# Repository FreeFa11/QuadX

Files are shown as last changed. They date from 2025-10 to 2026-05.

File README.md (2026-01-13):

# QuadX
A small Drone designed to be simple and cheap and not require a physical controller. It can be controlled by any Smartphone or Computer through Wifi connection using a web browser. 

## Project Outline
- <B>Firmware:</B> Flight Controller and Sensors
- <B>Hardware:</B> Schematic, PCB and 3D Files
- <B>Webpage:</B> Controller Webpage Files

## [Frame](./Hardware/Frame/)

<p align="center">
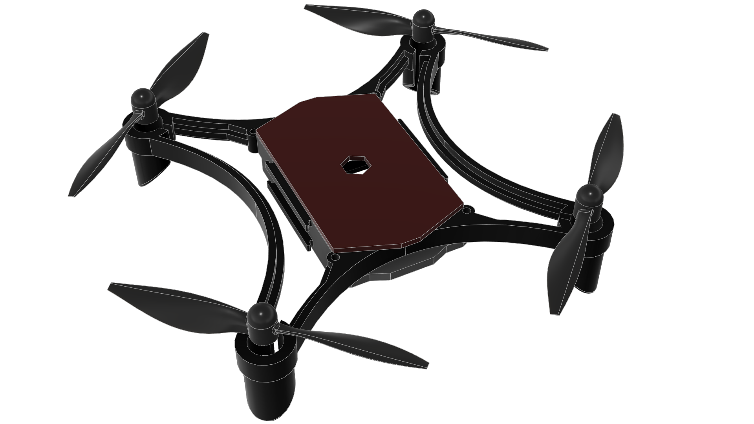
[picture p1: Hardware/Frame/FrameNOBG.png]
    
</p>

3D printed drone frame designed to easily hold 8mm diameter coreless motors and the custom Flight Controller [Board](./Hardware/PCB/).

## [PCB](./Hardware/PCB/)

<p align="center">
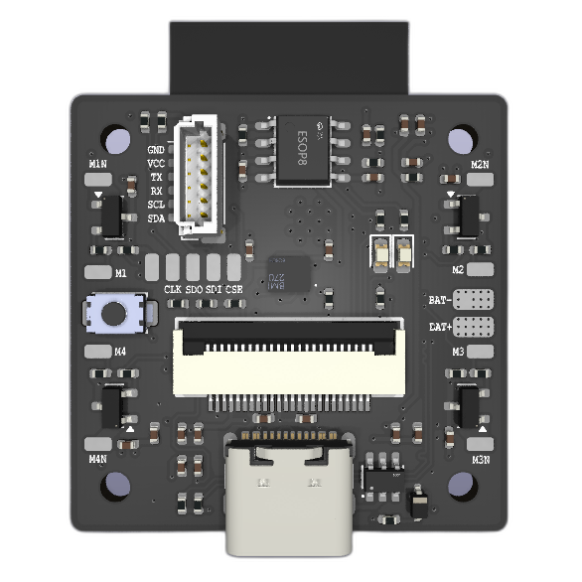
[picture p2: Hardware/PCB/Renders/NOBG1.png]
    
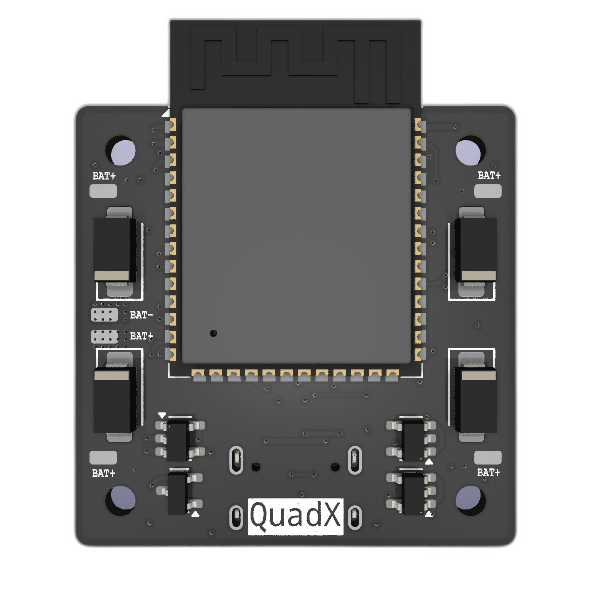
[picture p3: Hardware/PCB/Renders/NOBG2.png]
    
</p>

### Features

- ESP32S3 Microncontroller
- Onboard BMI160 IMU
- Onboard AO3416 MOSFETS
- Onboard Camera Connector
- Onboard 1S Battery Charger

External GPS + Compass module can be connected using the JST-SH (1.00 mm) connector.

## [Firmware](./Firmware/)

The Firmware has been developed using PlatformIO. This Firmware shares a lot of code with my [TwinBlade](https://github.com/FreeFa11/TwinBlade) project.

- **Build**: Open the [Firmware](./Firmware/) folder with PlatformIO installed and build:
  ```
  platformio run
  ```
  Build the filesystem that contains all the required files:
  ```
  platformio run --target buildfs
  ```

- **Flash**: Connect the target microcontroller to flash and run:
  ```
  platformio run --target uploadfs
  ```
  After flashing the filesystem, flash the firmware with:
  ```
  platformi run --target upload
  ```

- **Connect**: After the firmware has been successfully flashed, the microcontroller will act as a Wifi access point with the name `QuadX`. Connect your smartphone to it with password `letsrock`. Open your web browser and type the URL `quadx.local`. This will connect you to the webserver and load the webpage where you can control and modify the drone and its settings.

  *`quadx.local` only works in Wifi AP mode*

<br>

The Web Interface has mostly been completed in terms of functionality. Still needs some work in terms of UI. 
<p align="center">
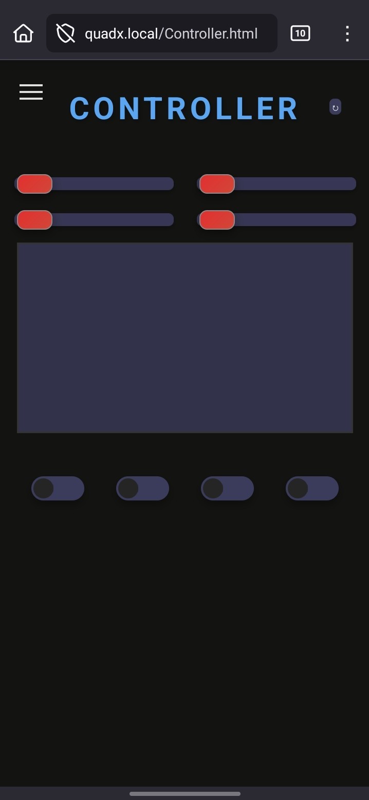
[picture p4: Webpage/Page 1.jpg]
    
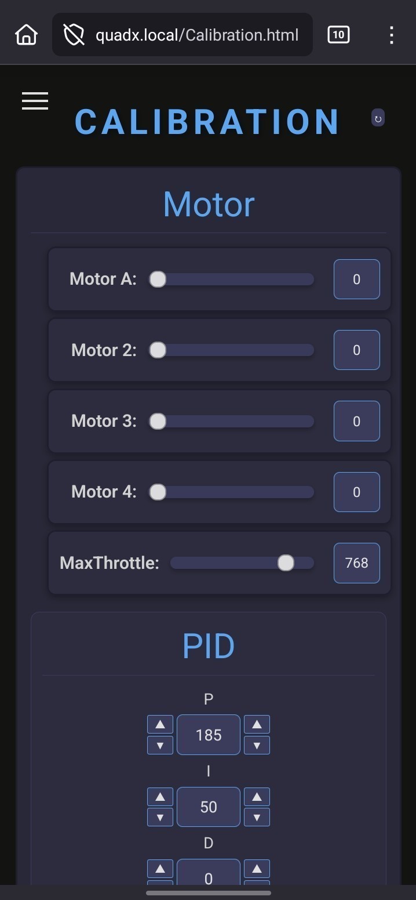
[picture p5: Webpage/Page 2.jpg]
    
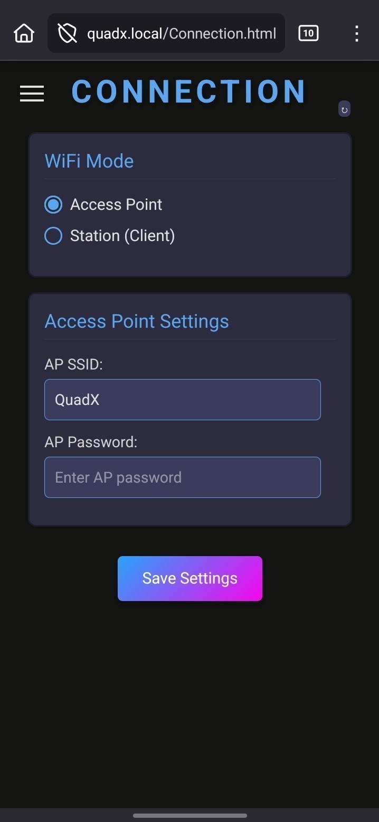
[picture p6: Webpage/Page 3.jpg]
    
</p>

PID gains and controller sensitivity can be easily adjusted from the web interface along with the Wifi settings.

## TODO
- Improve Firmware and Controller
- Real Time Camera Support
- Position and Altitude Hold
- DIY Optical Flow from Camera

## License

All the files in [Hardware](./Hardware/) folder are licensed under [CERN OHL-P v2](./Hardware/LICENSE).

All other files are licensed under [BSD 3-Clause](./LICENSE).

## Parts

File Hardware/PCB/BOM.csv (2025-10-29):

Designator | Footprint | Quantity | Value | LCSC Part #
C1, C10, C11, C12, C13, C17, C19, C2, C4, C5, C8, C9 | C_0402 | 12 | 1uF | C52923
C14, C15 | C_0402 | 2 | 10uF | C15525
C16, C18, C20, C21, C3, C6, C7 | C_0402 | 7 | 100nF | C1525
D1, D2, D3, D4 | D_SMA | 4 | SS34 | C8678
D5 | SOT-23-6_L2.9-W1.6-P0.95-LS2.8-BL-1 | 1 | SRV05-4_C7420376 | C7420376
D6 | D_0603 | 1 | Blue | C2286
D7 | D_0603 | 1 | Red | C2286
D8 | D_SOD-323 | 1 | BZT52C2V7S | C22375298
IC1 | BMI270 | 1 | BMI270
J1, J10, J11, J12, J14, J15, J17, J18, J19, J2, J22, J23, J24, J3, J4, J6, J7, J8, J9 | SolderWirePad_1x01_SMD_1x2mm | 19 | Conn_01x01
J13 | FPC-SMD_24P-P0.50_05A20L24P | 1 | Conn_01x26 | C5362158
J16 | USB_C_Receptacle_GCT_USB4105-xx-A_16P_TopMnt_Horizontal | 1 | USB_C_Receptacle_USB2.0_16P
J20, J21 | SolderWirePad_1x01_SMD_1.5x3mm | 2 | Conn_01x01
J5 | JST_SH_BM06B-SRSS-TB_1x06-1MP_P1.00mm_Vertical | 1 | Conn_01x06_MountingPin
Q1, Q2, Q3, Q4 | SOT-23 | 4 | AO3416
Q5 | Q_SOT-23 | 1 | AO3401A | C15127
R1, R11, R12, R13, R14, R15, R16, R17, R18, R19, R21, R23, R24, R4, R5, R6 | R_0402 | 16 | 10kΩ | C25744
R10, R2, R22, R3, R9 | R_0402 | 5 | 100Ω | C25076
R20 | R_0402 | 1 | 2kΩ | C4109
R7, R8 | R_0402 | 2 | 5.1kΩ | C25905
S1 | SW_TS-1088-AR02016 | 1 | Tactile Button, 160gf | C720477
U1 | SOT-23-5 | 1 | ME6211C28M5
U2 | SOT-23-5 | 1 | ME6211C15M5
U3 | SOT-23-5 | 1 | ME6211C33M5
U4 | ESOP-8_L4.9-W3.9-P1.27-LS6.0-BL-EP | 1 | TP4056 | C16581
U5 | ESP32-S3-WROOM-1 | 1 | ESP32-S3-WROOM-1

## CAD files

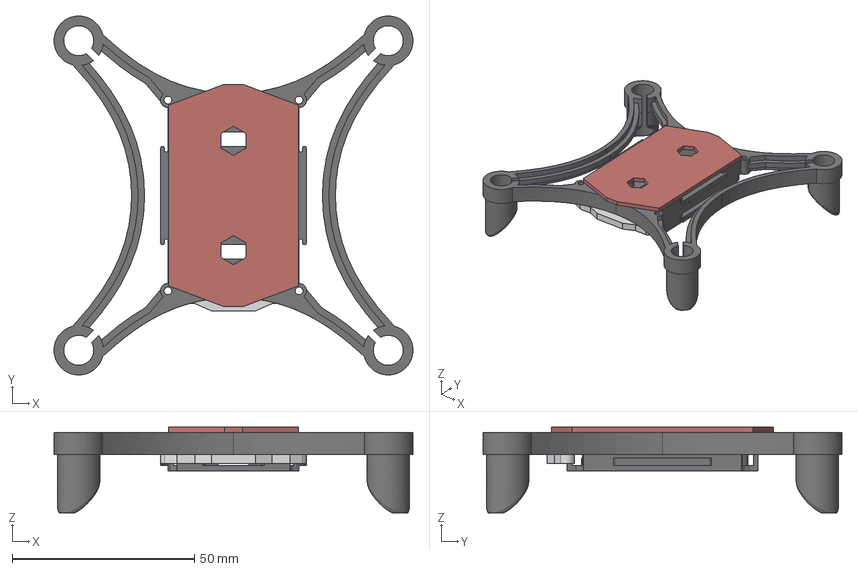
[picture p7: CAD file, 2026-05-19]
Hardware/Frame/Assembled.step
98.6 x 98.6 x 23.5 mm

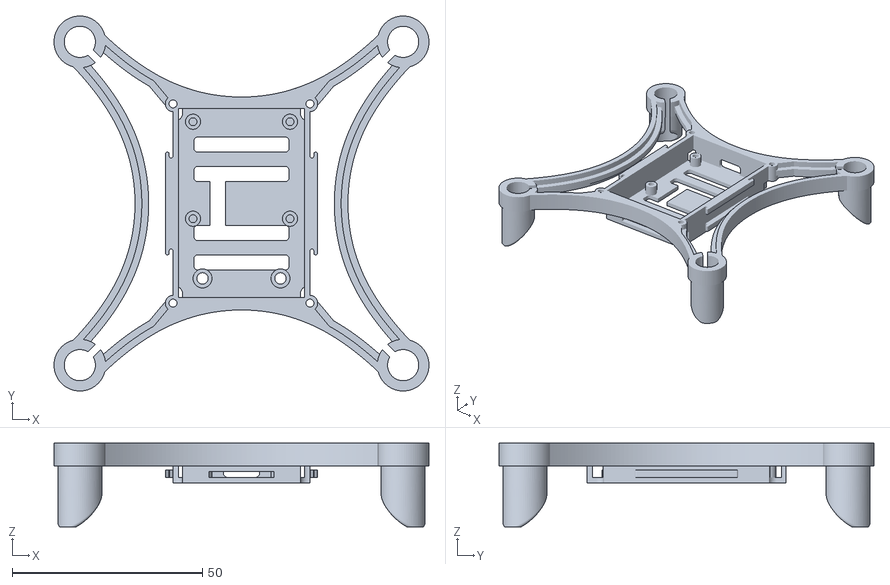
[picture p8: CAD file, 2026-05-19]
Hardware/Frame/Frame.stl
98.6 x 98.6 x 22.0

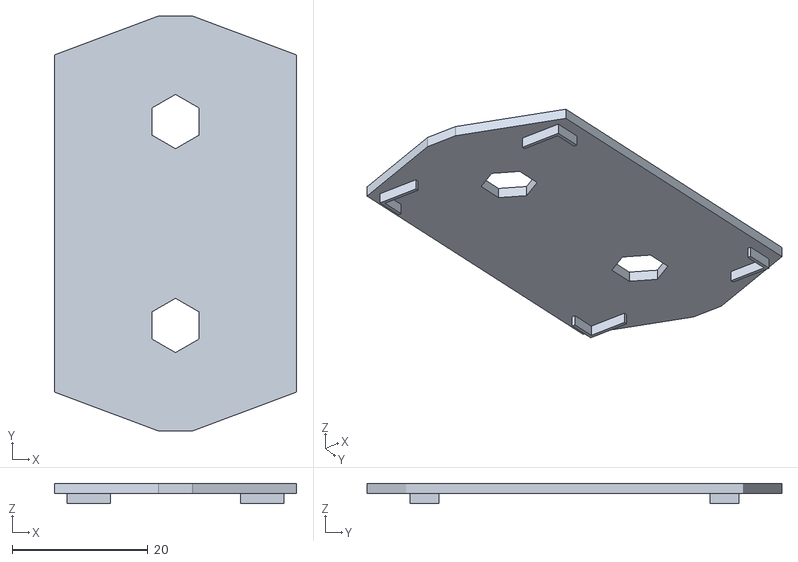
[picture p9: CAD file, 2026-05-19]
Hardware/Frame/Lid.stl
35.7 x 61.1 x 3.00

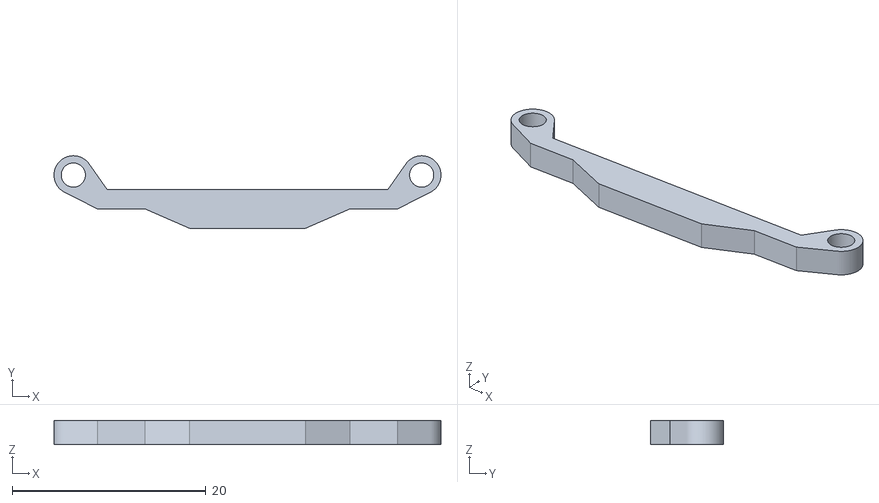
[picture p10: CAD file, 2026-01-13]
Hardware/Frame/Mount.stl
40.0 x 7.50 x 2.50

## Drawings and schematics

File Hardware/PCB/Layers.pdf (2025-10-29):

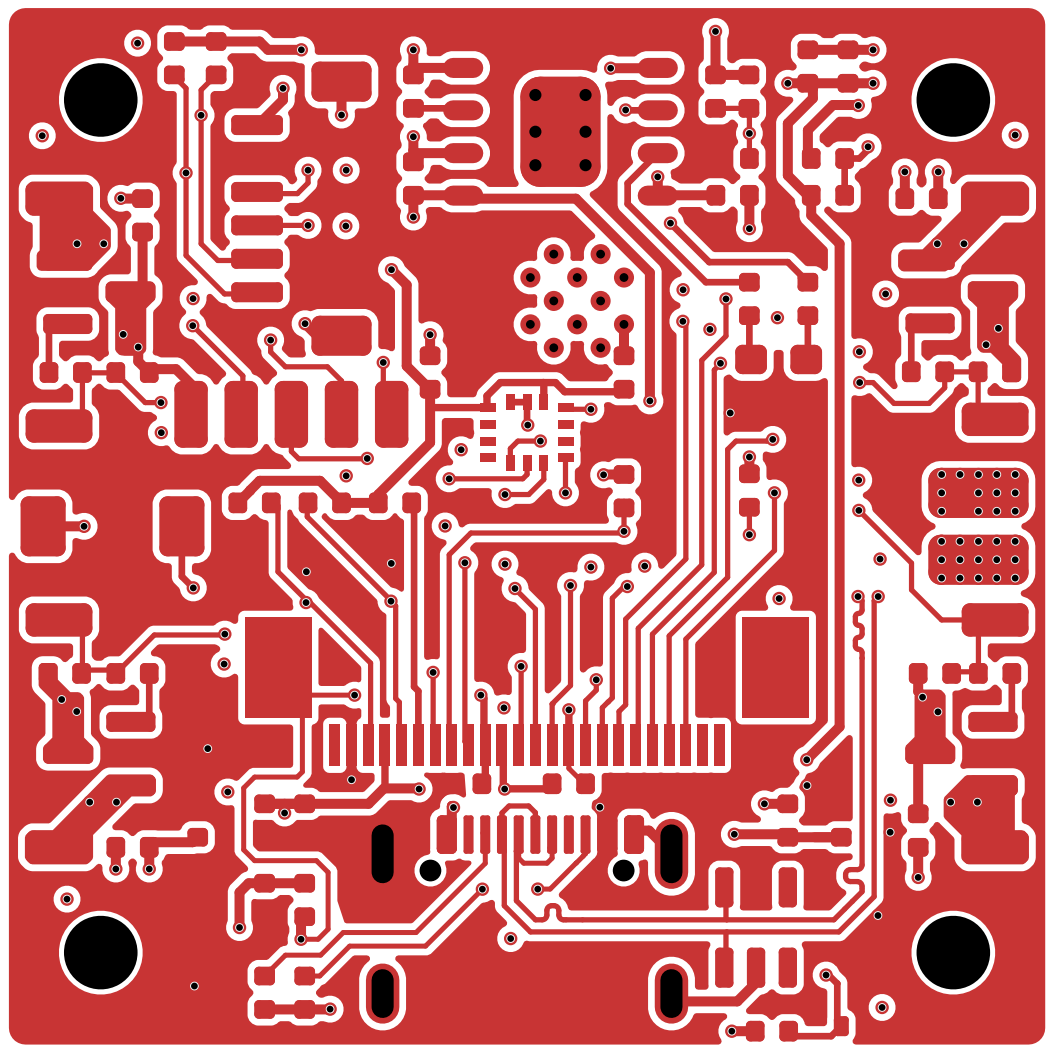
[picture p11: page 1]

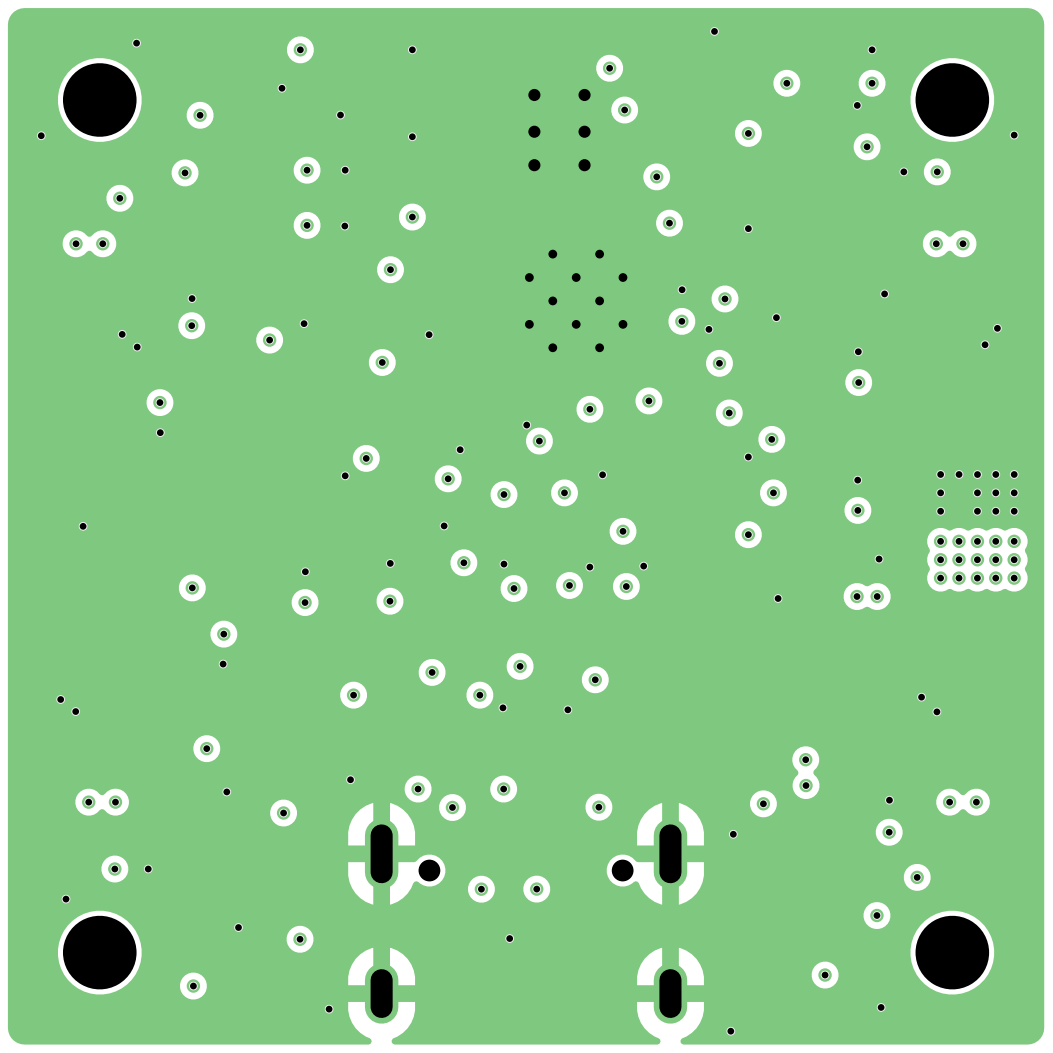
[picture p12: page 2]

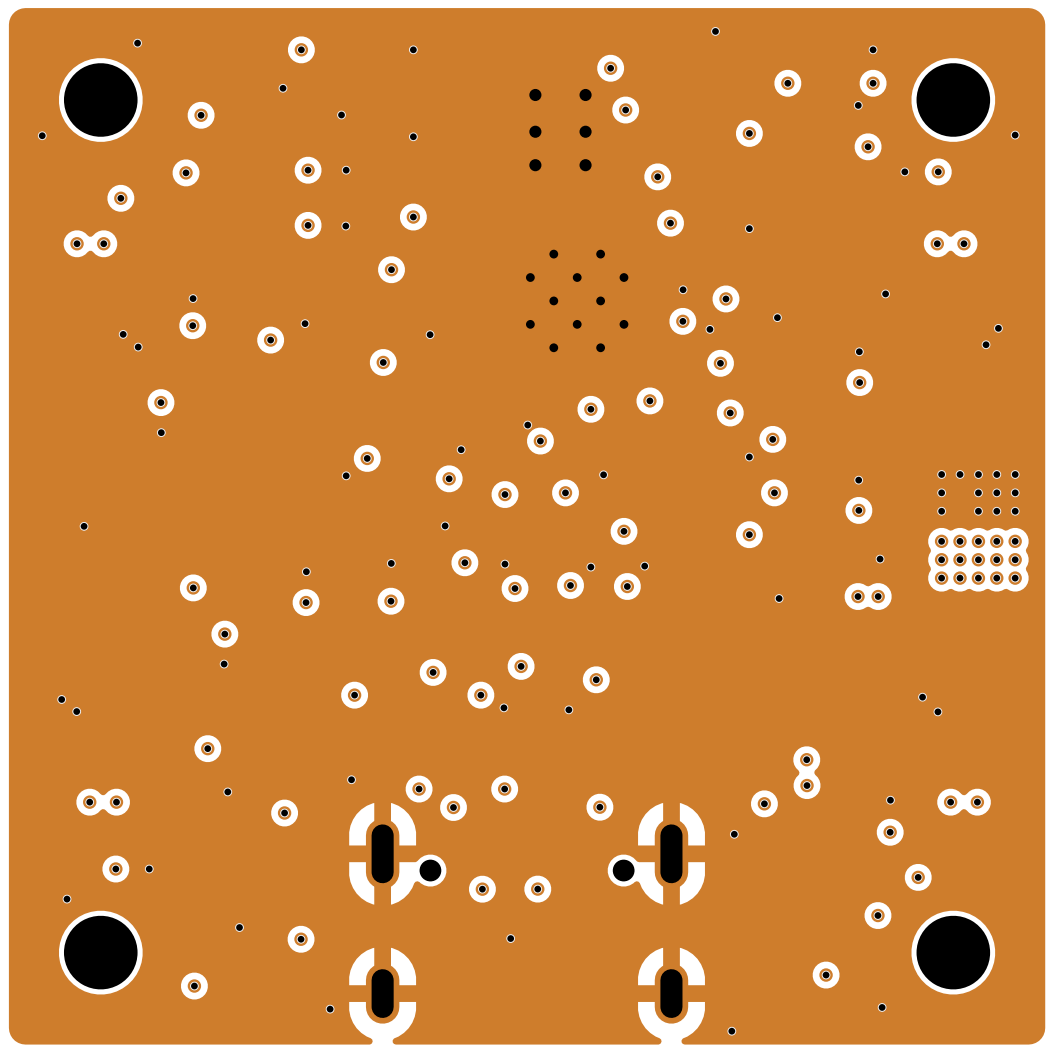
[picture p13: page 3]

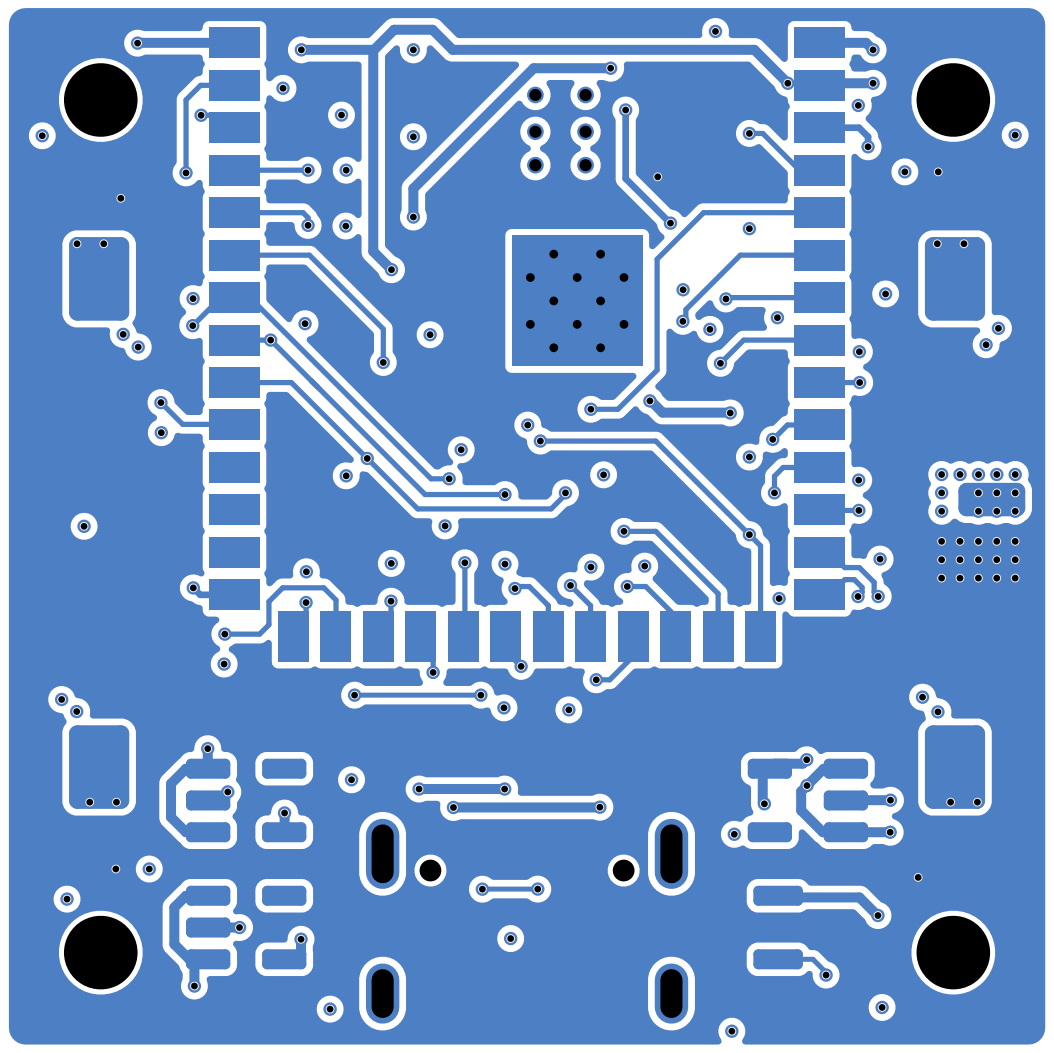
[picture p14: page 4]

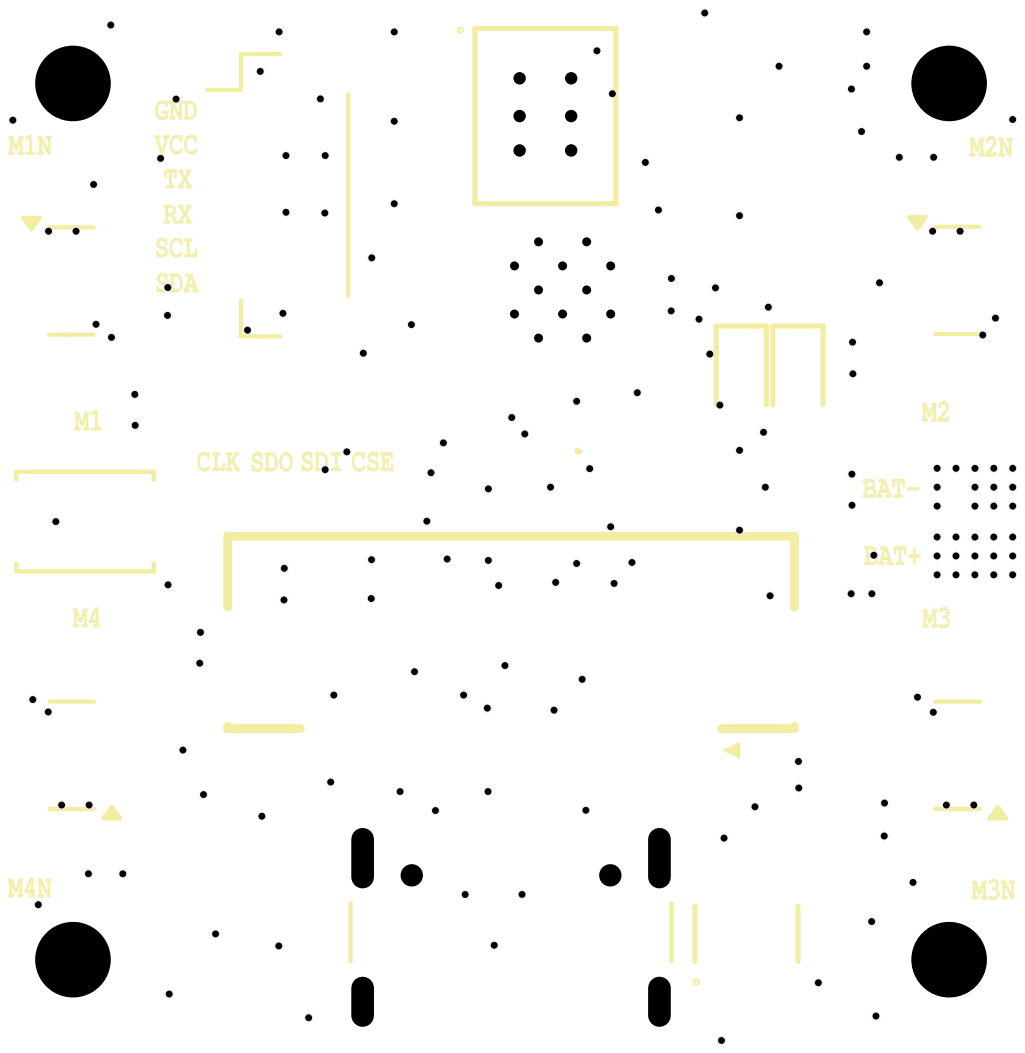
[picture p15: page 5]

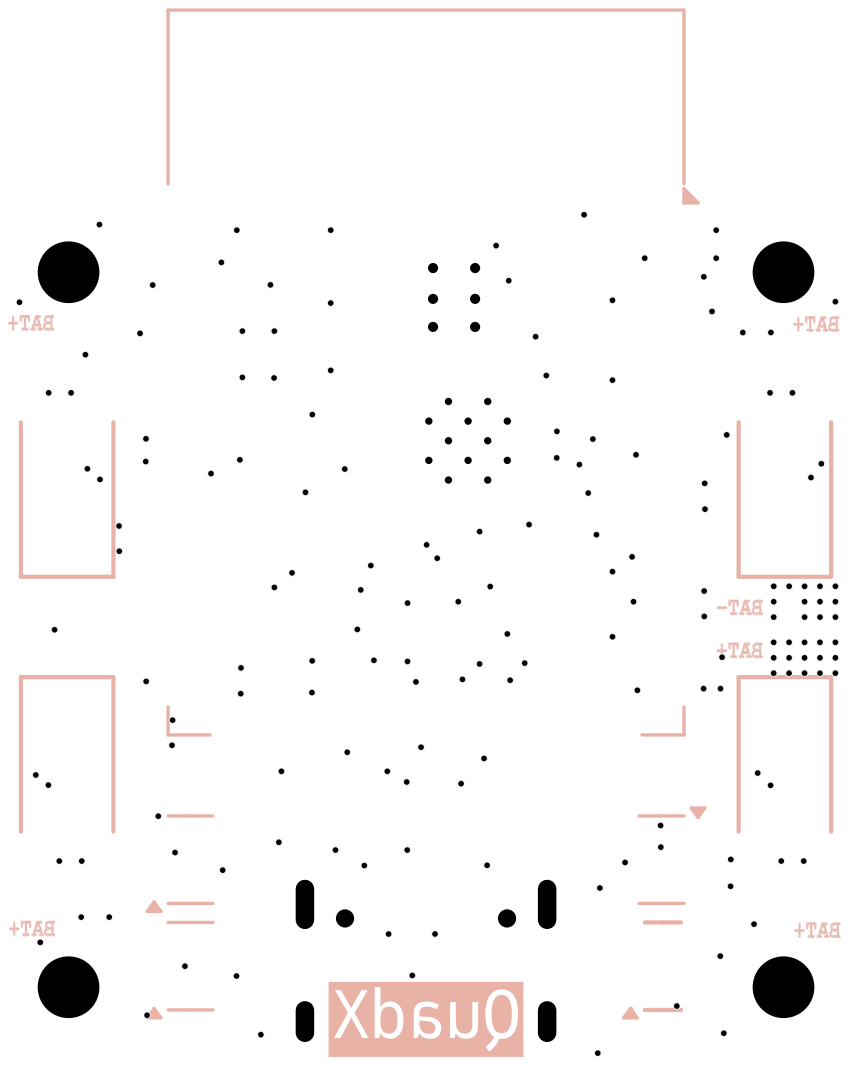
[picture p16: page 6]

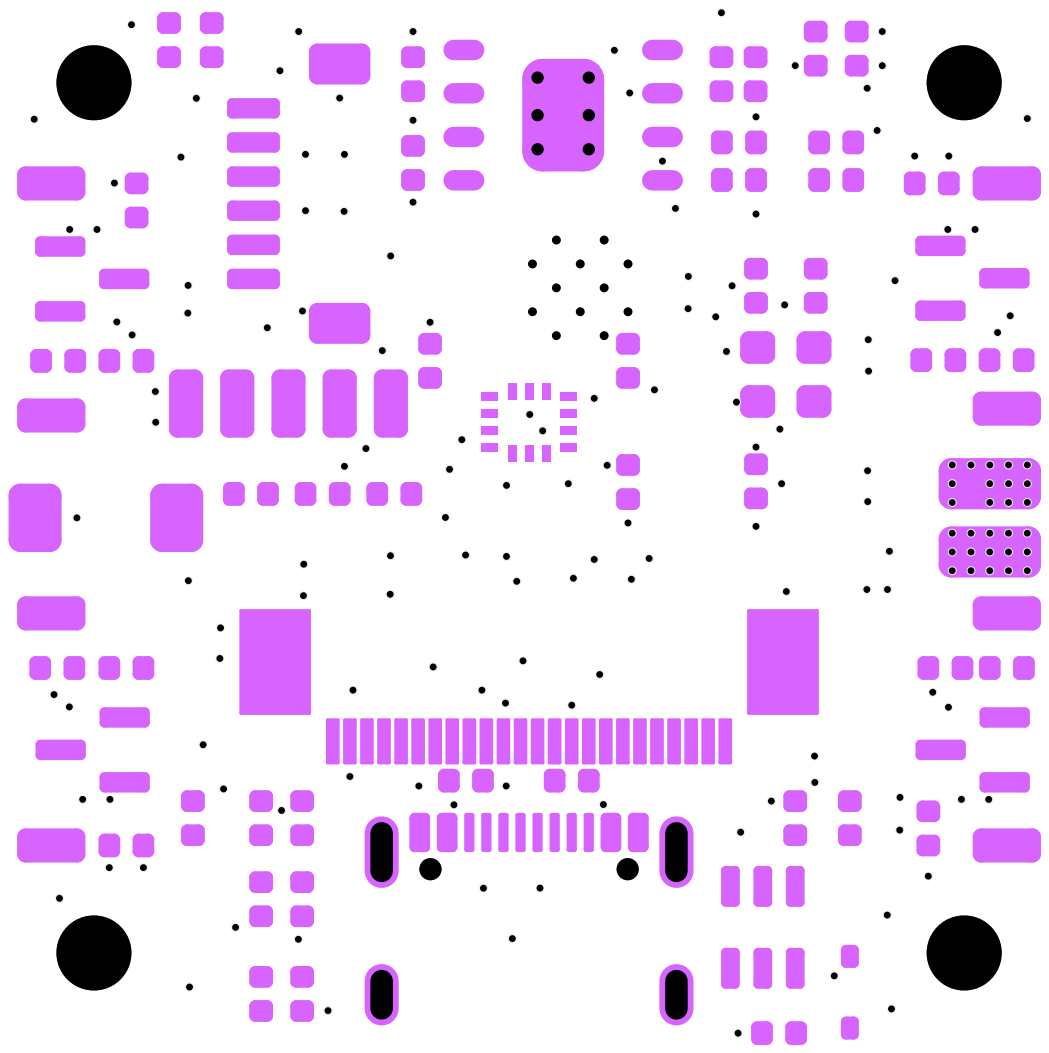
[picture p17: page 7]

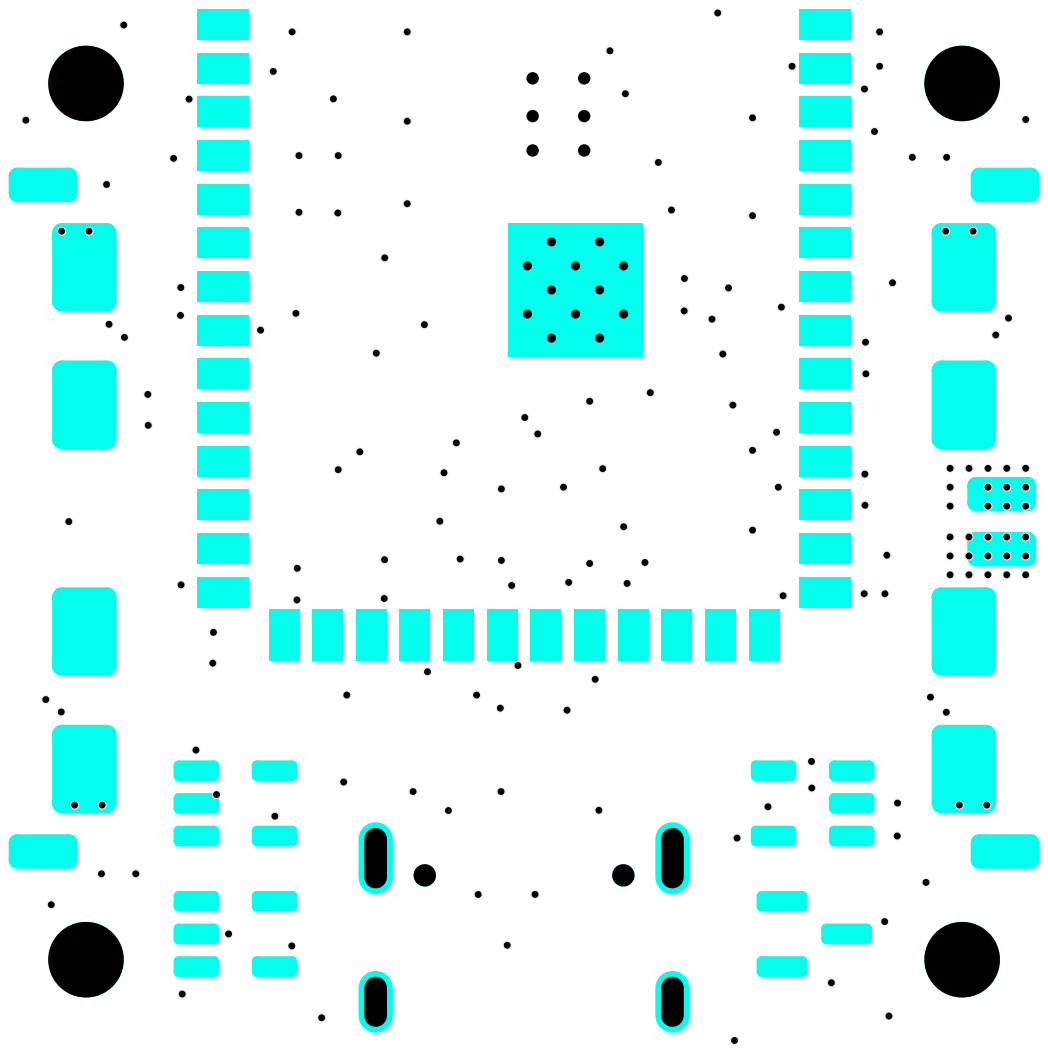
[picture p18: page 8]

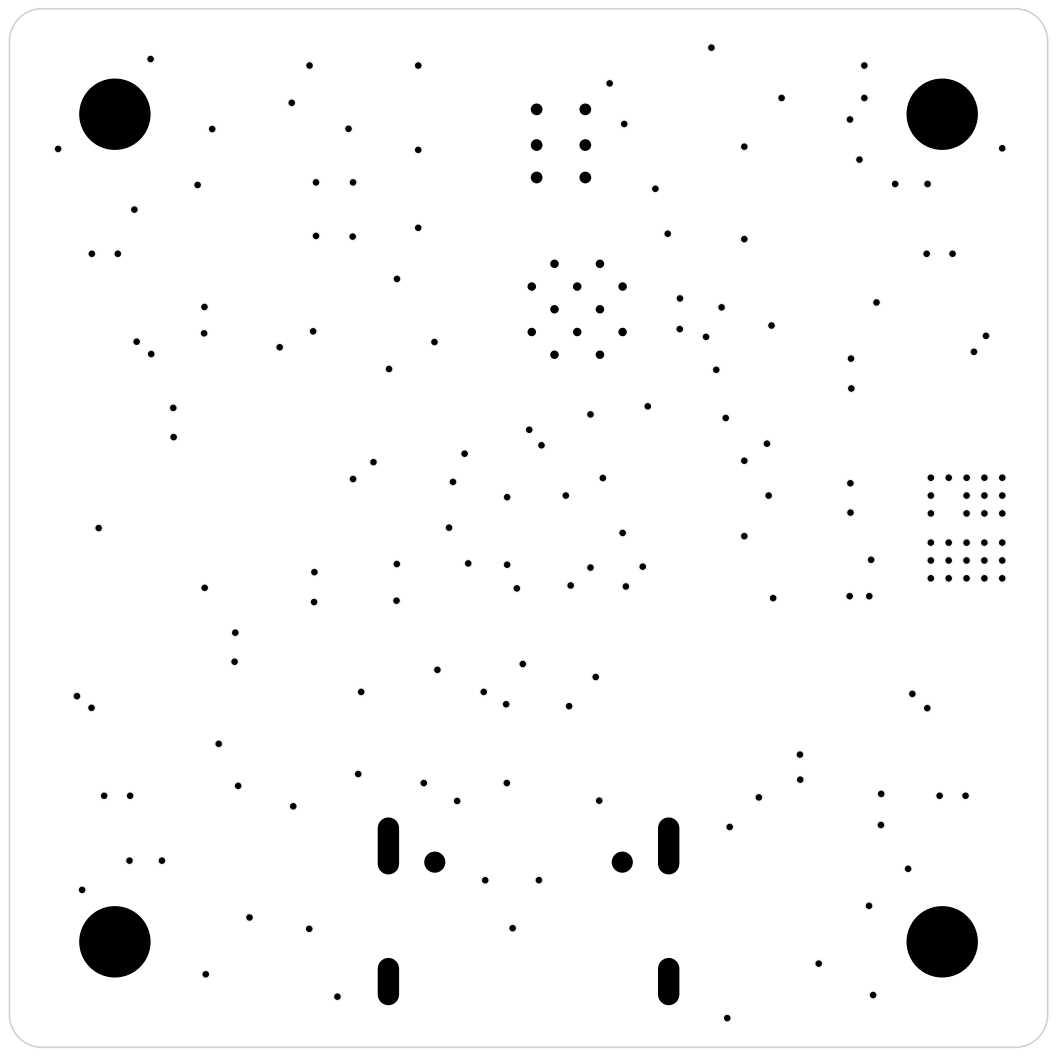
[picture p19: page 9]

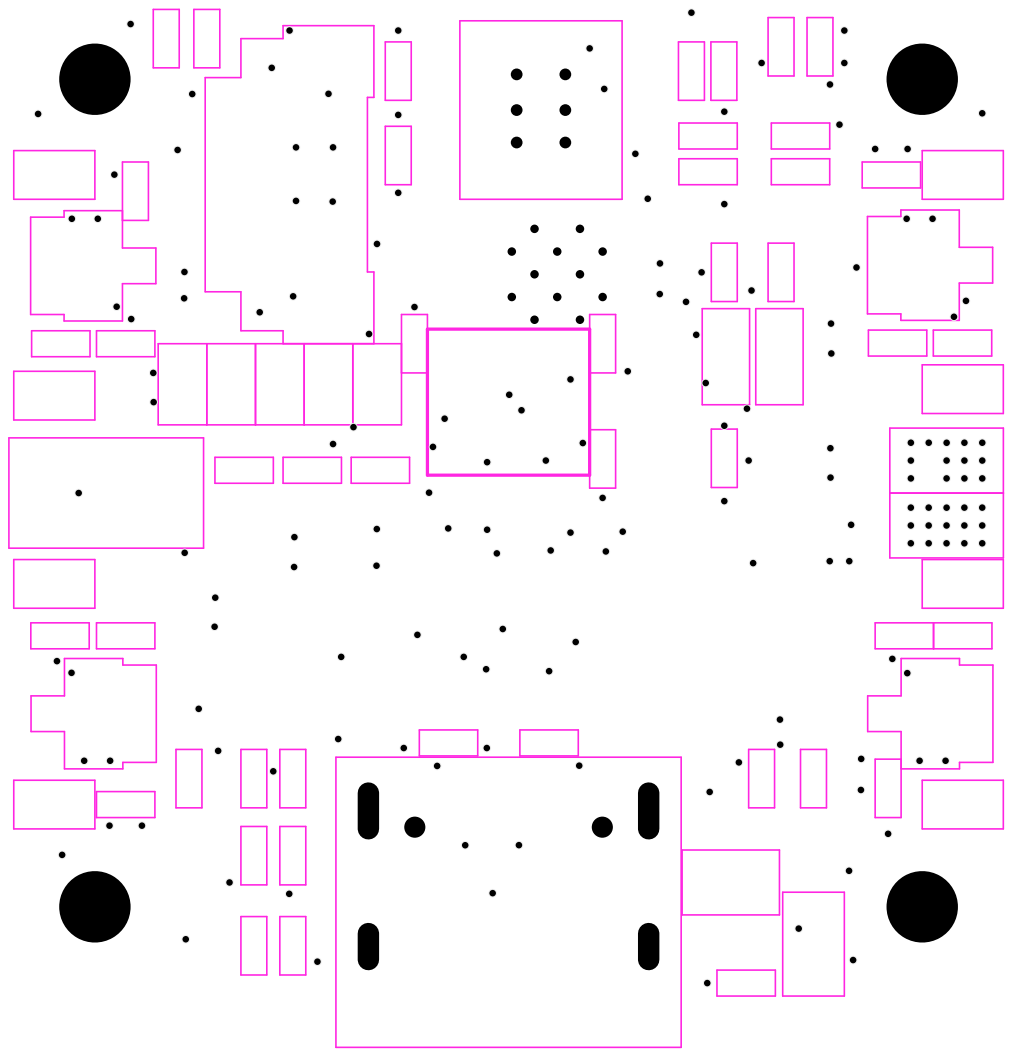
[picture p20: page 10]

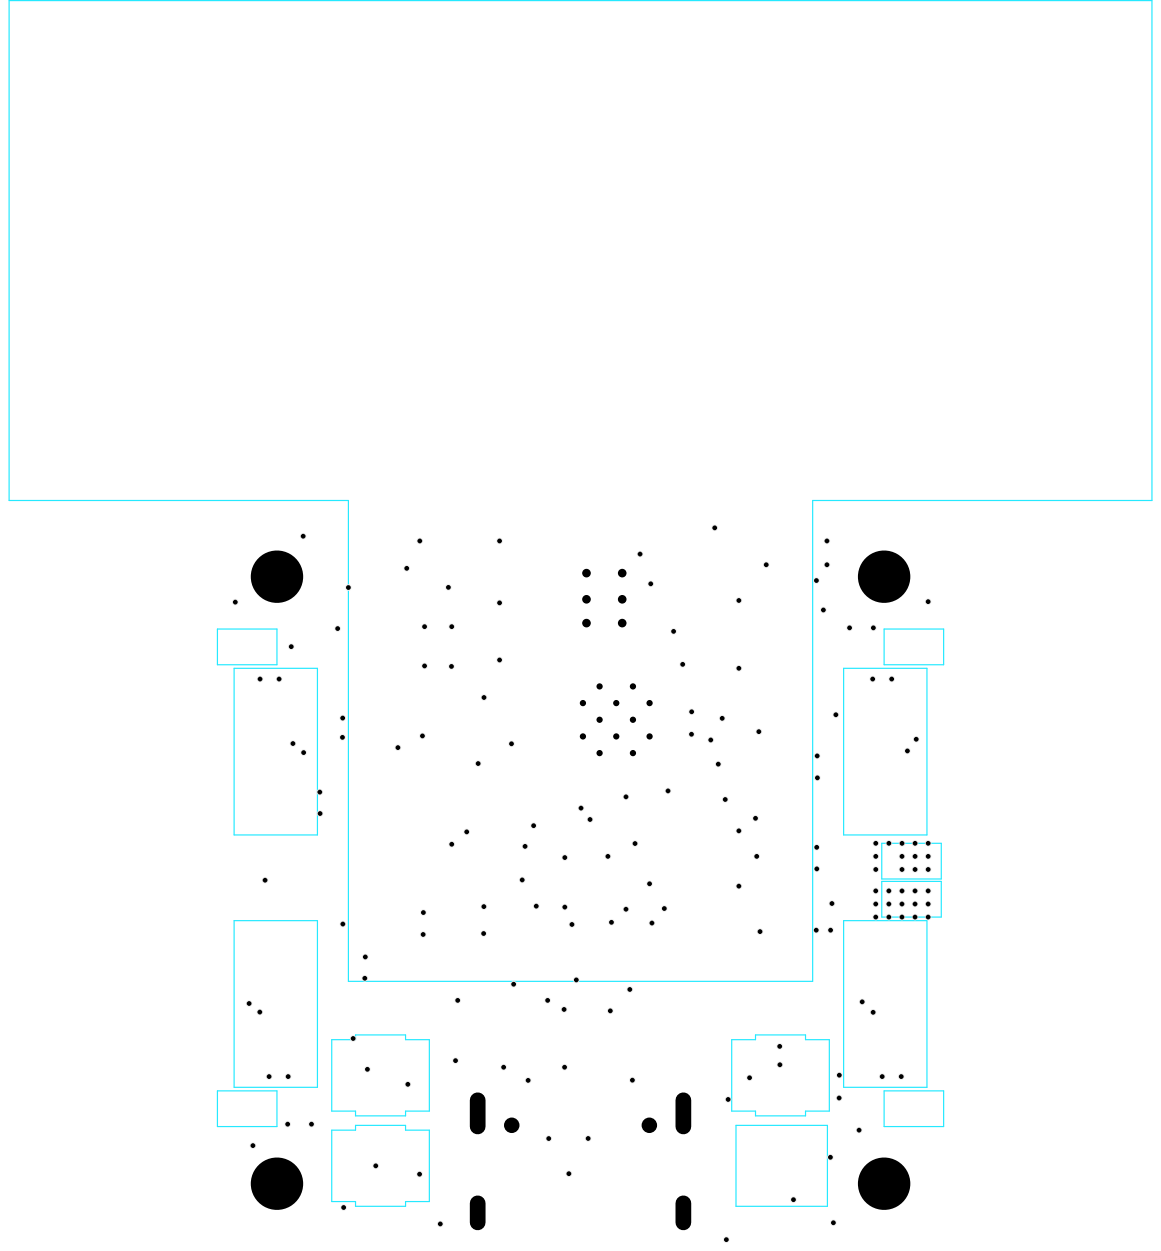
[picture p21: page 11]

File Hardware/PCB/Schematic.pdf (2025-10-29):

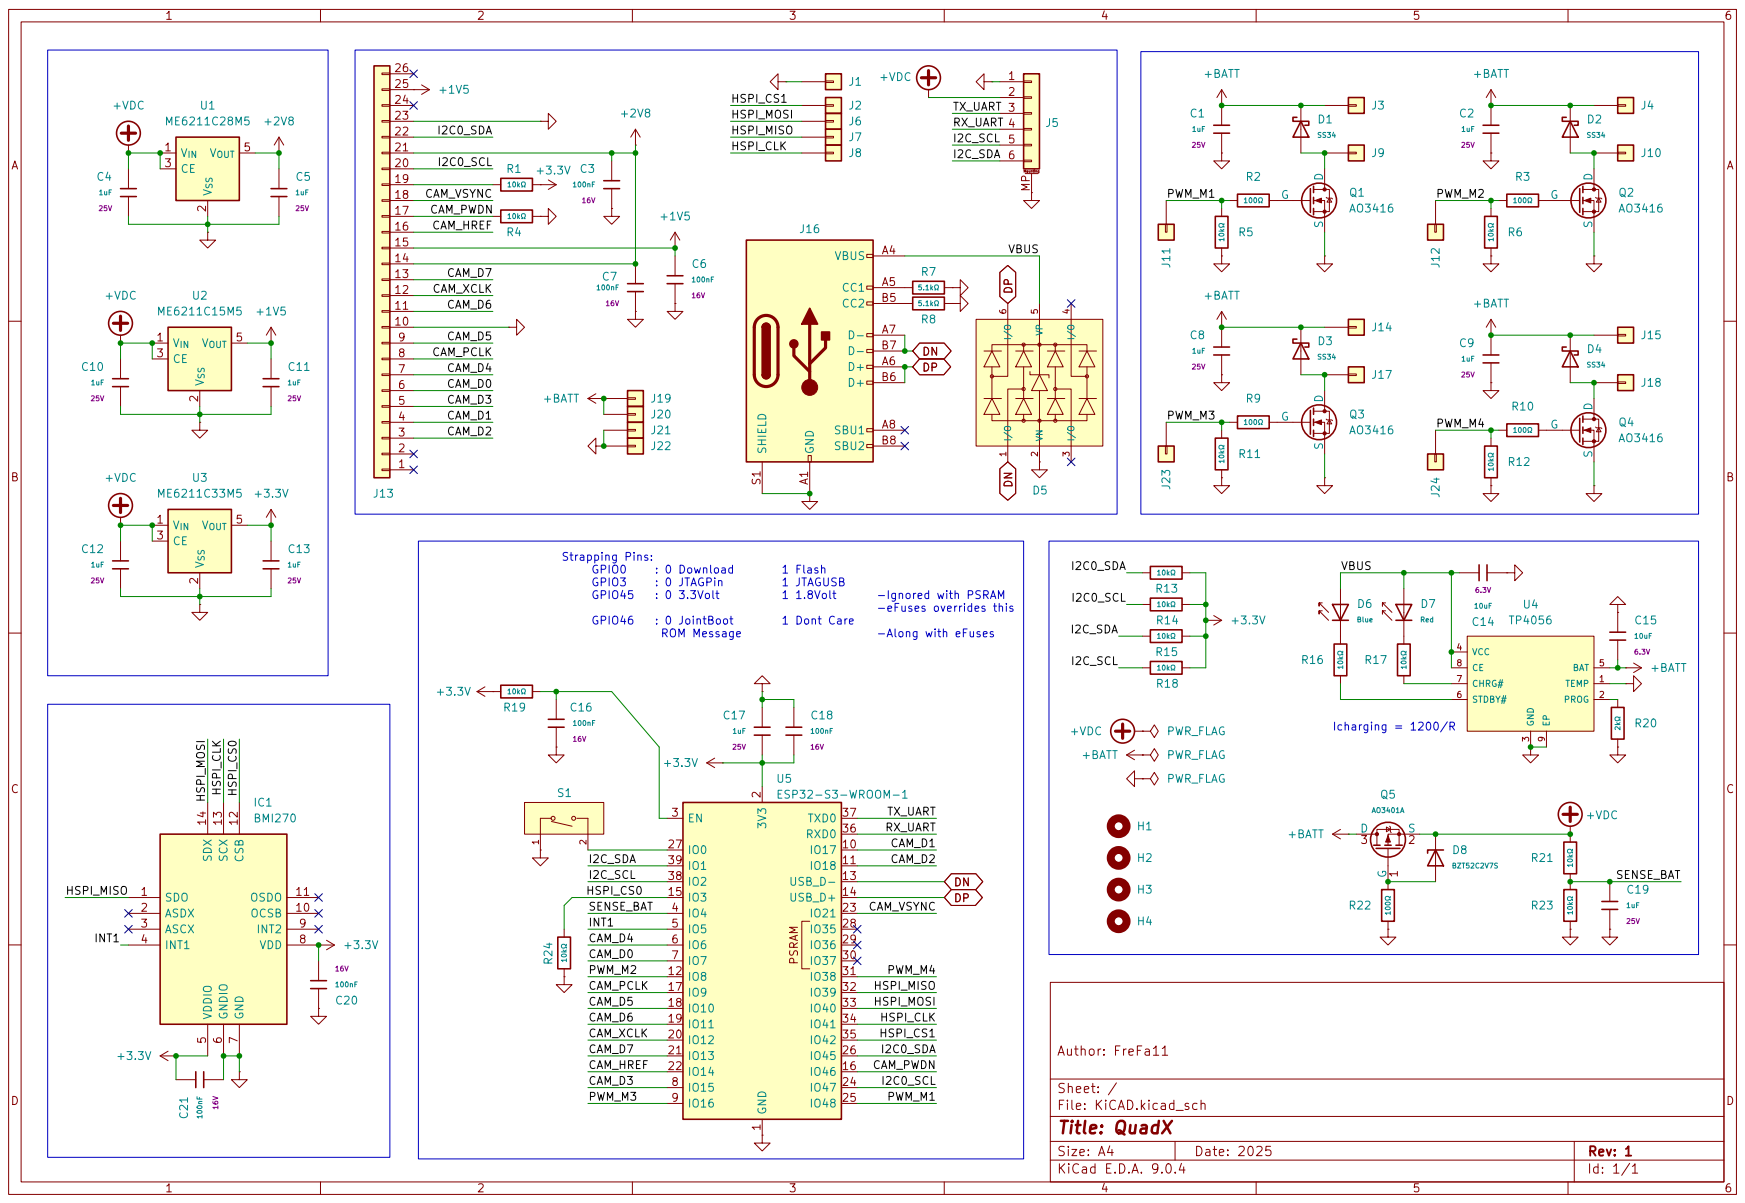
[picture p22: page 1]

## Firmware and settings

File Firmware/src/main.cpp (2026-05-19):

#include <Arduino.h>
#include <freertos/FreeRTOS.h>
#include <USB.h>
#include <LittleFS.h>
#include <Preferences.h>
#include <esp_now.h>

// Modular Codes
#include <Motor.h>
#include <Sensor.h>
#include <Webserver.h>
#include <Transmitter.h>
#include <Control.h>


// Task Handles & Functions
void SystemTask(void *param);
TaskHandle_t ControllerTask;
void Blinky(void *param);
TaskHandle_t BlinkyTask;
hw_timer_t *timer_sensor = NULL;
Webserver droneWebserver;

static void IRAM_ATTR onTimerSensor(){
    BaseType_t xHigherPriorityWoken = pdFALSE;
    vTaskNotifyGiveFromISR(ControllerTask, &xHigherPriorityWoken);
    if (xHigherPriorityWoken == pdTRUE) {portYIELD_FROM_ISR();}
}



// All the Initializations
void setup()
{
  USBSerial.begin(115200);
  LittleFS.begin();

// Wifi & Server
  droneWebserver.StartWiFi();
  droneWebserver.StartWebserver();

  // Transmitter
  StartReciever();

  // Test Sensor
  // Sensor<float> droneSensor;
  // droneSensor.InitializeIMU();
  // droneSensor.InitializeBARO();
  // droneSensor.StartSensors();
  // while(true){delay(1000);}


//  Tasks
  // xTaskCreatePinnedToCore(
  //   Blinky,
  //   "Blinky",
  //   1000,
  //   NULL,
  //   3,
  //   &BlinkyTask,
  //   0
  // );

  
  xTaskCreatePinnedToCore(
    SystemTask,
    "SystemTask",
    6000,
    NULL,
    3,
    &ControllerTask,
    1
  );  
}
void loop(){vTaskDelete(NULL);}
void Blinky(void *param)
{
  uint8_t LEDS[3] = {0, 0, 0};
  uint8_t CountColor;
  uint16_t Delay = 300, CountDelay = 4;
  
  // Builtin NEOPIXEL LED 10
  pinMode(10, OUTPUT);
  
  while(true)
  {
    for (int i = 0; i < CountDelay; ++i)
    {
      for (int i = 0; i < 3; ++i)
      {
        LEDS[i] = 0;
      }

      LEDS[CountColor] = 64;
      neopixelWrite(10, LEDS[0], LEDS[1], LEDS[2]);
      vTaskDelay(Delay / portTICK_RATE_MS);

      neopixelWrite(10, 0, 0, 0);
      vTaskDelay(Delay / portTICK_RATE_MS);

      CountColor++;
      CountColor %= 3;
    }
   
    CountDelay += CountDelay;
    Delay -= (Delay)/2;
    if (Delay < 30){Delay = 500; CountDelay = 4;}
  }
}




// ************************************************ Flight System ******************************************* //

void SystemTask(void *param)
{ 
  // Hardware Timer for accuracy
  timer_sensor = timerBegin(0, 80, true);       // 1 MHz
  timerAttachInterrupt(timer_sensor, &onTimerSensor, true);
  timerAlarmWrite(timer_sensor, TimerRateModeCount, true);

  System mySystem(State::Flight);
  mySystem.Start();
}


void System::FlightHandle()
{
  // Peripheral Objects
  Sensor<float> droneSensor;
  Quaternion<float> droneAttitude;
  Motor droneMotor;
  CalibrationData droneSettings;
  ControllerData remoteInput;         // remoteInput Buffer
  
  // Control System Objects
  uint8_t counter=0;
  uint16_t altitude_counter=0;
  float InputPitch=0, InputRoll=0, InputYaw=0;
  Quaternion<float> DesiredAngle, ErrorAngle;
  PID pid_roll, pid_pitch, pid_yaw;
  float DesiredGX=0, DesiredGY=0, DesiredGZ=0;
  Quaternion<float> DesiredRateBodyFrame;
  float ErrorGX=0, ErrorGY=0, ErrorGZ=0;
  PID pid_gx, pid_gy, pid_gz;
  float CorrectedGX=0, CorrectedGY=0, CorrectedGZ=0;
  
  // CalibrationData
  ReadCalibration(droneSettings);
  pid_roll.SetGain(1, 0.05, 0);
  pid_pitch.SetGain(1, 0.05, 0);
  pid_yaw.SetGain(1, 0.05, 0);
  pid_roll.SetIntegralLimit(.5);
  pid_pitch.SetIntegralLimit(.5);
  pid_yaw.SetIntegralLimit(.5);
  pid_roll.SetControlFrequency(TimerAngleModeFreq);
  pid_pitch.SetControlFrequency(TimerAngleModeFreq);
  pid_yaw.SetControlFrequency(TimerAngleModeFreq);
  pid_gx.SetGain(droneSettings.P, droneSettings.I, droneSettings.D);
  pid_gy.SetGain(droneSettings.P, droneSettings.I, droneSettings.D);
  pid_gz.SetGain(droneSettings.P, droneSettings.I, droneSettings.D);
  pid_gx.SetIntegralLimit(150);
  pid_gy.SetIntegralLimit(150);
  pid_gz.SetIntegralLimit(150);
  pid_gx.SetControlFrequency(TimerRateModeFreq);
  pid_gy.SetControlFrequency(TimerRateModeFreq);
  pid_gz.SetControlFrequency(TimerRateModeFreq);
  

  // Initialization
  droneSensor.InitializeIMU();
  #ifdef HAS_MAGNETOMETER
  droneSensor.InitializeMAG();
  #endif
  #ifdef HAS_BAROMETER
  droneSensor.InitializeBARO();
  #endif
  droneMotor.InitializeMotor();
  timerAlarmEnable(timer_sensor);

  

  while(xQueueIsQueueEmptyFromISR(StateQueue))
  {
    // Wait for Hardware Timer Notification
    ulTaskNotifyTake(pdTRUE, portMAX_DELAY);

    // Update Data and Counter
    droneSensor.UpdateIMUData();
    droneSensor.NormalizeVectors();
    counter += 1;


    // ** Angle Control **//
    if(counter >= TimerModeSwitchCount)
    {
      counter = 0;

      // Update Attitude
      droneAttitude.UpdateMahony(droneSensor);
      // droneAttitude.UpdateMadgwick(droneSensor);

      if (!xQueueIsQueueEmptyFromISR(ControllerQueue))
      {
        // New Data from Queues
        xQueueReceive(ControllerQueue, &remoteInput, 0);

        // Convert Input Command
        InputRoll=remoteInput.JoystickX2/1023.f          * MAX_ROLL_RADIAN;
        InputPitch=remoteInput.JoystickY2/1023.f         * MAX_PITCH_RADIAN;
        InputYaw -= 0.02f*remoteInput.JoystickX1/1023.f  * MAX_YAW_RAD_SEC;
        if (InputYaw >  M_PI) InputYaw -= 2.0f * M_PI;
        if (InputYaw < -M_PI) InputYaw += 2.0f * M_PI;
        
        // Angle in Quaternion
        float cr = cosf(InputRoll  * 0.5f);
        float sr = sinf(InputRoll  * 0.5f);
        float cp = cosf(InputPitch * 0.5f);
        float sp = sinf(InputPitch * 0.5f);
        float cy = cosf(InputYaw   * 0.5f);
        float sy = sinf(InputYaw   * 0.5f);
  
        // Euler --> quaternion
        DesiredAngle.w = cy*cp*cr + sy*sp*sr;
        DesiredAngle.x = cy*cp*sr - sy*sp*cr;
        DesiredAngle.y = cy*sp*cr + sy*cp*sr;
        DesiredAngle.z = sy*cp*cr - cy*sp*sr;
      }
      
      // Error Attitude
      ErrorAngle = DesiredAngle.inverse()*droneAttitude*2.0f;
      ErrorAngle = (ErrorAngle.w < 0)? ErrorAngle*(-1): ErrorAngle;
      
      // PID Angle Corrected Rates
      DesiredGX = - pid_roll.Update(ErrorAngle.x);  // World Frame
      DesiredGY = - pid_pitch.Update(ErrorAngle.y);
      DesiredGZ = - pid_yaw.Update(ErrorAngle.z);
      
      // USBSerial.printf("%.4f,%.4f,%.4f,%.4f\n", DesiredAngle.w, DesiredAngle.x, DesiredAngle.y, DesiredAngle.z);        
      // USBSerial.printf("%.4f,%.4f,%.4f,%.4f\n", droneAttitude.w, droneAttitude.x, droneAttitude.y, droneAttitude.z);     
      // USBSerial.printf(">X:%.4f\n>Y:%.4f\n>Z:%.4f\n", DesiredGX, DesiredGY, DesiredGZ);
    }

    // altitude_counter += 1;
    // if (altitude_counter >= TimerAltitudeCount) {
    //   altitude_counter = 0;
      // droneSensor.UpdateBAROData();
    // }
    
    USBSerial.printf(">X:%.2f\n>Y:%.2f\n>Z:%.2f\n", droneSensor.GX, droneSensor.GY, droneSensor.GZ);    
    
    //** Rate Control **//
    // Actuation is done in body frame. Desired World Rate -> Desired Body Rate
    DesiredRateBodyFrame = droneAttitude.inverse()*Quaternion<float>(0,DesiredGX,DesiredGY,DesiredGZ)*droneAttitude;
    // ErrorGX = DesiredRateBodyFrame.x - droneSensor.GX;
    // ErrorGY = DesiredRateBodyFrame.y - droneSensor.GY;
    // ErrorGZ = DesiredRateBodyFrame.z - droneSensor.GZ;
    ErrorGX = 0 - droneSensor.GX;
    ErrorGY = 0 - droneSensor.GY;
    ErrorGZ = 0 - droneSensor.GZ;
    CorrectedGX = pid_gx.Update(ErrorGX);
    CorrectedGY = pid_gx.Update(ErrorGY);
    CorrectedGZ = pid_gx.Update(ErrorGZ);


    if (remoteInput.Toggle1){
      // Mixer
      droneMotor.A  = Clamp(uint16_t(droneSettings.motorA + remoteInput.Slider1*5 + CorrectedGX + CorrectedGY - CorrectedGZ), uint16_t(0), uint16_t(droneSettings.maxthrottle));
      droneMotor.B  = Clamp(uint16_t(droneSettings.motorB + remoteInput.Slider1*5 + CorrectedGX - CorrectedGY + CorrectedGZ), uint16_t(0), uint16_t(droneSettings.maxthrottle));
      droneMotor.C  = Clamp(uint16_t(droneSettings.motorC + remoteInput.Slider1*5 - CorrectedGX - CorrectedGY - CorrectedGZ), uint16_t(0), uint16_t(droneSettings.maxthrottle));
      droneMotor.D  = Clamp(uint16_t(droneSettings.motorD + remoteInput.Slider1*5 - CorrectedGX + CorrectedGY + CorrectedGZ), uint16_t(0), uint16_t(droneSettings.maxthrottle));
      droneMotor.ActuateMotor();
    }
    else{
      droneMotor.UpdateMotor(0,0,0,0);
      droneMotor.ActuateMotor();
    }      
  }

  // Disable the Motors
  droneMotor.UpdateMotor(0,0,0,0);
  droneMotor.ActuateMotor();
  timerAlarmDisable(timer_sensor);
}

void System::CalibrationHandle()
{
  CalibrationData newData;
  Motor droneMotor;

  while(xQueueIsQueueEmptyFromISR(StateQueue))
  {
    if (xQueueReceive(CalibrationQueue, &newData, 0))
    {
      if (newData.save) {
          SaveCalibration(newData);
        }
      else {
          droneMotor.UpdateMotor(newData.motorA, newData.motorB, newData.motorC, newData.motorD);
          droneMotor.ActuateMotor();
        }      
    }

    vTaskDelay(5 / portTICK_PERIOD_MS);
  }

  // Disable the Motors
  droneMotor.UpdateMotor(0,0,0,0);
  droneMotor.ActuateMotor();
}

void System::ConnectionHandle()
{
  while(xQueueIsQueueEmptyFromISR(StateQueue))
  {
    vTaskDelay(10 / portTICK_PERIOD_MS);   
  }
}

void System::UpdateState()
{
  xQueueReceive(StateQueue, &(this->currentState), 0);
}

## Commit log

2025-10-29 Added PCB Files
    [Accelero.csv, BOM.csv]
2025-12-12 Sensor Fusion and Controller
    [Partitions.csv]
2026-01-11 Flight Control Integration
    [Accelero.csv]
2026-01-13 Update Frame Design
    [Assembled.step, Frame.stl, GuardA.stl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]
2026-05-19 Updated Firmware for PCB
    [Assembled.step, Frame.stl, Lid.stl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]
